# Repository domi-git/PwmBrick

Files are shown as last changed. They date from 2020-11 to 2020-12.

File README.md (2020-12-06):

# PwmBrick

The aim of the project is to create a little box to control a DC-motor. The power should come from a 18650 LiIon-cell and the form-factor should be small.

**This is not a finished product! If you use anything from the project, you use it at your own risk! Be especially careful with the handling of LiIon-Batteries! If you don't know what you're doing there is always the risk of a thermal runaway which could lead to a fire or an explosion!**

## Overview

The current state of the prototype can be seen in the following picture:

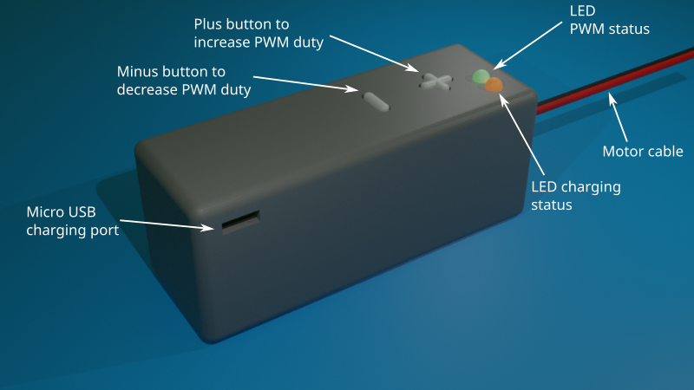
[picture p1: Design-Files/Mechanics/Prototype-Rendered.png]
Prototype-Render


**Main Features:**

| Feature | Value |
|---|---|
| Max. Output Current | 3A |
| Output Voltage (depends on charging status) | 3.4V - 4.2V |
| PWM-States (Can be switched via the buttons) | 4 |
| PWM frequency | 10kHz |
| Undervoltage Lockout (going into) | 3.4V |
| Undervoltage Lockout (leaving) | 3.7V |

## Mechanics

All the CAD-Drawings were carried out with Blender. The assembly consists of the following parts:
* top-part of the housing with cutouts for the buttons, the charging port and the LEDs
* bottom-part of the housing
* fibre-optics to guide the LED light
* plus- and minus-button
* pcb with soldered battery-holder for 18650-cell

You can see the listed parts in the following picture:

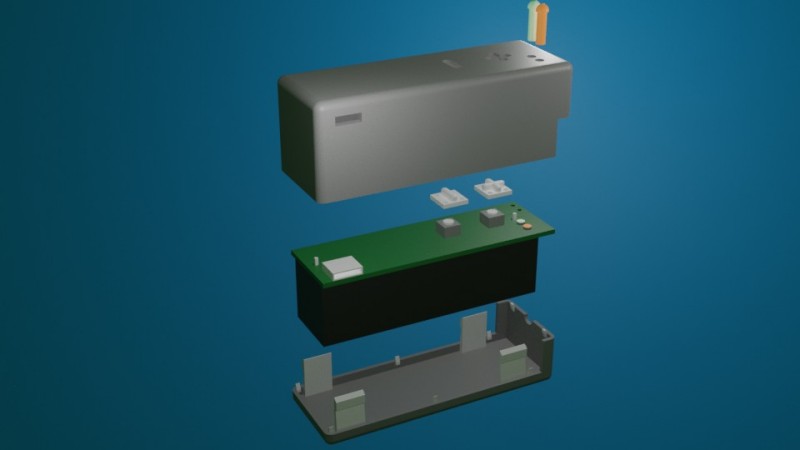
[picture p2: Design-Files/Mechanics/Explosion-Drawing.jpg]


## Electronics

The schematic and the layout was done in KiCad. The goal was to keep the overall space of the electronics very close to the footprint of the battery-holder for the 18650 LiIon cell. 

**Block diagram**

Schematic

**Schematic**

Schematic

**Layout**

Layout-Top
Layout-Bot

## Software

TBD

## Possible improvements

### Documentation
* Snap-Fit Design
* The states of the PWM
* Debugging capabilities with TermControl
* How to flash new software

### Mechanics

* Incoporate a cutout for the micro-usb charging port. At the moment the cable does not fit.

### Electronics

For the current PCB:
* Accurately measure the undervoltage lockout thresholds
* Measure the charging current over time

For next PCB revision:
* Incorporate a way to use the charging LED from the microcontroller (It should not be exclusive to the charging IC)
* Low-pass for the measurement of the battery-voltage
* Pull-Downs/Pull-Ups for the Uart/Flash connector

### Software   

* Clean up the code
* Implement a soft transition of the pwm duty-cycle in state changes
* Replace as much of generated code from the IDE with own implementations

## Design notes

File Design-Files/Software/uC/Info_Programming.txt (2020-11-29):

The controller can be programmed via ST-Link/V2-1. You can use most of the nucleo boards from ST for programming, because they have an integreted programmer (i have the Nucleo-F446RE-Board).

Connection between Nucleo-Board and own PCB
-------------------------------------------
I'm using connector CN4 on the Nucleo-Board, with the following pins:
- VDD
- SWCLK
- GND
- SWDIO
- NRST

You can flash the software with the STM32CubeIDE (just press the "debug"-button).

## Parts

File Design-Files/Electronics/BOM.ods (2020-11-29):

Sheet: Übersicht
Part | MPN | Quantity | Price | Price (sum) | Height | Area mmxmm (incl. Pins) | Link
Microcontroller | STM32F030F4P6 | 1 | 1.40 € | 1.40 € | 1.0 | 6.5x6.5 | https://www.reichelt.de/mcu-arm-32-bit-16-kb-tssop-20-stm-32f030f4p6-p168428.html?&trstct=pos_4
Mosfets | SI4114DY-GE3 | 2 | 0.87 € | 1.74 € | 1.8 | 4.9x6.0 | https://www.reichelt.de/mosfet-n-ch-20v-20a-0-006r-so8-si4114dy-ge3-p254848.html?&trstct=pol_1
Mosfet-Driver | IR2011S | 1 | 2.30 € | 2.30 € | 1.8 | 4.9x6.0 | https://www.reichelt.de/mosfet-treiber-high-and-low-side-so-8-ir-2011s-p129748.html?&trstct=pos_07
Boost-Converter | MAX5026EUT+T | 1 | 1.10 € | 1.10 € | 1.5 | 3.0x3.0 | https://www.reichelt.de/boost-schaltregler-adj-40ma-3-11vi-sot23-6-max5026eut-t-p256372.html?trstct=pol_10
Inductor | L-PIS2408 10µ | 1 | 0.74 € | 0.74 € | 3.2 | 6.6x6.2 | https://www.reichelt.de/smd-power-induktivitaet-pis2408-ferrit-10-l-pis2408-10-p73080.html?trstct=pol_5
Boost Diode | MBR0520LT1 | 1 | 0.08 € | 0.08 € | 1.3 | 2.8x1.8 | https://www.reichelt.de/schottkydiode-20-v-0-5-a-sod-123-mbr-0520lt1g-ons-p219620.html?&trstct=pol_0
Linear Regulator (3.3V) | MCP1700T-2502E/TT | 1 | 0.53 € | 0.53 € | 1.0 | 2.1x2.6 | https://www.conrad.de/de/p/microchip-technology-mcp1700t-2502e-mb-pmic-spannungsregler-linear-ldo-positiv-fest-sot-89-3-1085862.html
Charging-IC | MAX1811 | 1 | 2.75 € | 2.75 € |  |  | https://www.reichelt.de/battery-management-ic-li-lader-so-8-max-1811-esa-p57853.html?&trstct=pos_1
LED orange | KA-3528SECKT | 1 | 0.12 € | 0.12 € | 1.9 | 2.8x3.5 | https://www.conrad.de/de/p/kingbright-ka-3528seckt-smd-led-plcc2-orange-230-mcd-120-20-ma-2-1-1050363.html
LED green | KA-3528CGCKT | 1 | 0.13 € | 0.13 € | 1.9 | 2.8x3.5 | https://www.conrad.de/de/p/kingbright-ka-3528cgckt-smd-led-plcc2-gruen-100-mcd-120-20-ma-2-1-v-1050365.html
Optical Fiber | 1282.1000 | 2 | 0.69 € | 1.38 € | - | - | https://www.conrad.de/de/p/mentor-1282-1000-hohllichtleiter-starr-kartenbefestigung-presspassung-183494.html
Button | RND 210-00203 | 2 | 0.21 € | 0.42 € | 4.3 | 6x6 | https://www.reichelt.de/printtaster-smd-1-57-n-6-x-6-x-4-3-mm-rnd-210-00203-p226424.html?trstct=pol_10
Programming heaeder THT 1.27mm vertically |  | 1 | 0.89 € | 0.89 € | 5.0 |  | https://www.conrad.de/de/p/tru-components-stiftleiste-standard-anzahl-reihen-1-polzahl-je-reihe-20-tc-2506255-1-st-2139366.html
Charging Jack (Micro-USB) |  | 1 | 1.96 € | 1.96 € | 2.6 |  | https://www.conrad.de/de/p/micro-usb-steckverbinder-serie-wr-com-buchse-einbau-vertikal-smt-wuerth-elektronik-inhalt-1-st-1898830.html
Capacitor | X7R-G0603 100N | 1 | 0.02 € | 0.02 € | 1.0 |  | https://www.reichelt.de/smd-vielschicht-keramikkondensator-100n-10-x7r-g0603-100n-p31873.html?trstct=pol_0
Capacitor | KEM X5R0603 1,0U | 1 | 0.02 € | 0.02 € | 1.0 |  | https://www.reichelt.de/vielschicht-kerko-1-0-f-25v-85-c-kem-x5r0603-1-0u-p207006.html?&trstct=pol_1
Capacitor | KEM X5R0603 4,7U | 4 | 0.07 € | 0.28 € | 1.0 |  | https://www.reichelt.de/vielschicht-kerko-4-7-f-10v-85-c-kem-x5r0603-4-7u-p207009.html?&trstct=pol_0
Quarz 8MHz | 8.000MHZ MQ 30/30/40/12PF | 1 | 2.21 € | 2.21 € | 1.2 | 5x7 | https://www.conrad.de/de/p/euroquartz-quarzkristall-quarz-smd-5x7-smd-4-8-000-mhz-12-pf-7-mm-5-mm-1-2-mm-1-st-155131.html
Capacitor 4pF Quarz | NPO 0603 CF 4,0P | 1 | 0.02 € | 0.02 € |  |  | https://www.reichelt.de/smd-kerko-0603-4-0pf-50v-10-mlcc-npo-0603-cf-4-0p-p193988.html?&trstct=pol_0
Fuse (not recommended, but footprint in PCB v4) | 220034 | 1 | 0.69 € | 0.69 € |  | 3x7 | https://www.conrad.de/de/p/eska-smd-ssq-f-3-a-smd-sicherung-smd-2410-3-a-125-v-flink-f-1-529794.html
Fuse (recommended and in use in PCB v4) | MINISMDC150F-2 | 1 | 0.04 € | 0.04 € |  |  | https://lcsc.com/product-detail/Surface-Mount-Fuses_TE-Connectivity_MINISMDC150F-2_1-5A-6V_C9308.html
Programming header THT 1.27mm horizontal | TC-1414-20-2-20-00 | 1 | 1.30 € | 1.30 € | 2.1 |  | https://www.conrad.de/de/p/w-p-products-stiftleiste-standard-anzahl-reihen-1-polzahl-je-reihe-20-707-1-20-2-20-00-1-719680.html
Resistor 0 Ohm | RND 0805 0 | 3 | 0.02 € | 0.06 € |  |  | https://www.reichelt.de/smd-widerstand-0805-0-ohm-125-mw-rnd-0805-0-p183146.html?&nbc=1
Various other Resistors in 0805, see schematic (I have them laying around)

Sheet: Lade-IC
Bauteil | MPN | Preis | Features | Bedenken | Link
Lade-IC | MAX1555 | 2.02 € | 100mA, Eingangsspannung OK, Ladestatus, UVLO-Eingang, 4.2V Full | Thermik? | https://www.conrad.de/de/p/maxim-integrated-max1555ezk-t-pmic-batteriemanagement-lademanagement-li-ion-li-pol-tsot-23-5-oberflaechenmontage-1121936.html
Lade-IC | MCP73833-FCI/UN | 0.86 € | Temp Monitor, Programmable Full-Voltage, CC und CV-Ladung, Programmable Charge Current, Ladestatus |  | https://www.conrad.de/de/p/microchip-technology-mcp73833-fci-un-pmic-batteriemanagement-lademanagement-li-ion-li-pol-msop-10-oberflaechenmontage-1085504.html
Lade-IC | MAX1811 | 2.75 € | 4.1/4.2 Full, Ladestatus, Enable, SO-8 Package, 100mA oder 500mA |  | https://www.reichelt.de/battery-management-ic-li-lader-so-8-max-1811-esa-p57853.html?&trstct=pos_1
Lade-IC | BQ24090 | 1.25 € | 100mA oder 500mA, Sicherheitstimer (10h), CC und CV-Ladung, Ausgangskurzschlusserkennung, Termistor Pin, Ladestatus, Power Good |  | https://www.reichelt.de/battery-management-ic-li-ion-msop-10-bq-24090-dgqt-p188799.html?trstct=pos_0
Lade-IC | MC34671AEPR2 | 1.39 € | 600mA, |  | https://www.conrad.de/de/p/nxp-semiconductors-mc34671aepr2-pmic-batteriemanagement-lademanagement-li-ion-li-pol-udfn-8-ep-2x3-oberflaechenmonta-1182980.html

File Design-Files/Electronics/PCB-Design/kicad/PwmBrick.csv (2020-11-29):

Id | Designator | Package | Quantity | Designation | Supplier and ref
1 | J1 | battery_holder_18650 | 1 | Conn_01x02
2 | R4,R13 | R_0805_2012Metric_Pad1.15x1.40mm_HandSolder | 2 | 270R
3 | TP2,TP1 | TestPoint_Pad_1.0x1.0mm | 2 | TestPoint
4 | R8,R12,R11 | R_0805_2012Metric_Pad1.15x1.40mm_HandSolder | 3 | 10k
5 | R7 | R_0805_2012Metric_Pad1.15x1.40mm_HandSolder | 1 | 120k
6 | R6 | R_0805_2012Metric_Pad1.15x1.40mm_HandSolder | 1 | 100k
7 | J4 | PinHeader_1x06_P1.27mm_Horizontal | 1 | Conn_01x06_Male
8 | F1 | Fuse_2512_6332Metric | 1 | Fuse
9 | R9,R10,R5 | R_0805_2012Metric_Pad1.15x1.40mm_HandSolder | 3 | 0R
10 | C15,C16,C9,C10,C17 | C_0603_1608Metric_Pad1.05x0.95mm_HandSolder | 5 | 100n
11 | U5 | SO-8_3.9x4.9mm_P1.27mm | 1 | IR2011
12 | C14,C8,C6,C5,C4 | C_0603_1608Metric_Pad1.05x0.95mm_HandSolder | 5 | 1u
13 | U4 | TSSOP-20_4.4x6.5mm_P0.65mm | 1 | STM32F030F4Px
14 | C7,C11,C2,C1 | C_0603_1608Metric_Pad1.05x0.95mm_HandSolder | 4 | 4u7
15 | C12,C13 | C_0603_1608Metric_Pad1.05x0.95mm_HandSolder | 2 | 4p
16 | Y1 | Crystal_SMD_EuroQuartz_MQ-4Pin_7.0x5.0mm | 1 | Crystal_GND24
17 | R3,R1 | R_0805_2012Metric_Pad1.15x1.40mm_HandSolder | 2 | 47k
18 | R2 | R_0805_2012Metric_Pad1.15x1.40mm_HandSolder | 1 | 330k
19 | Q2,Q1 | SOIC-8-SI4114DY-GE3 | 2 | Q_NMOS_DGS
20 | SW2,SW1 | SW_Push_1P1T_NO_6x6mm_H9.5mm | 2 | SW_Push
21 | U1 | TSOT-23-6 | 1 | MAX5026EUT
22 | J3 | Motor_Connector | 1 | Conn_01x02
23 | J2 | USB_Micro-B_Wuerth_629105150521 | 1 | USB_B_Micro
24 | L1 | L_6.3x6.3_H3 | 1 | 10u
25 | D4,D2 | LED_PLCC-2 | 2 | LED
26 | D1,D3 | D_SOD-123 | 2 | MBR0520LT
27 | U2 | SOT-89-3 | 1 | MCP1700-2502E_SOT89
28 | U3 | SOIC-8_3.9x4.9mm_P1.27mm | 1 | MAX1811

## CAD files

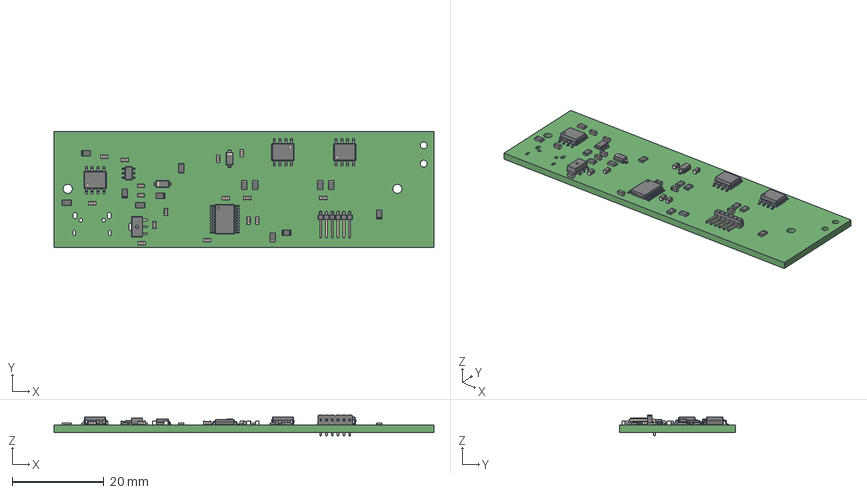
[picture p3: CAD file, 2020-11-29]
Design-Files/Mechanics/blender/kicad-export/pcb.step
83.0 x 25.3 x 4.50 mm
switch x 2

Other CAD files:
Design-Files/Mechanics/blender/assembly.blend

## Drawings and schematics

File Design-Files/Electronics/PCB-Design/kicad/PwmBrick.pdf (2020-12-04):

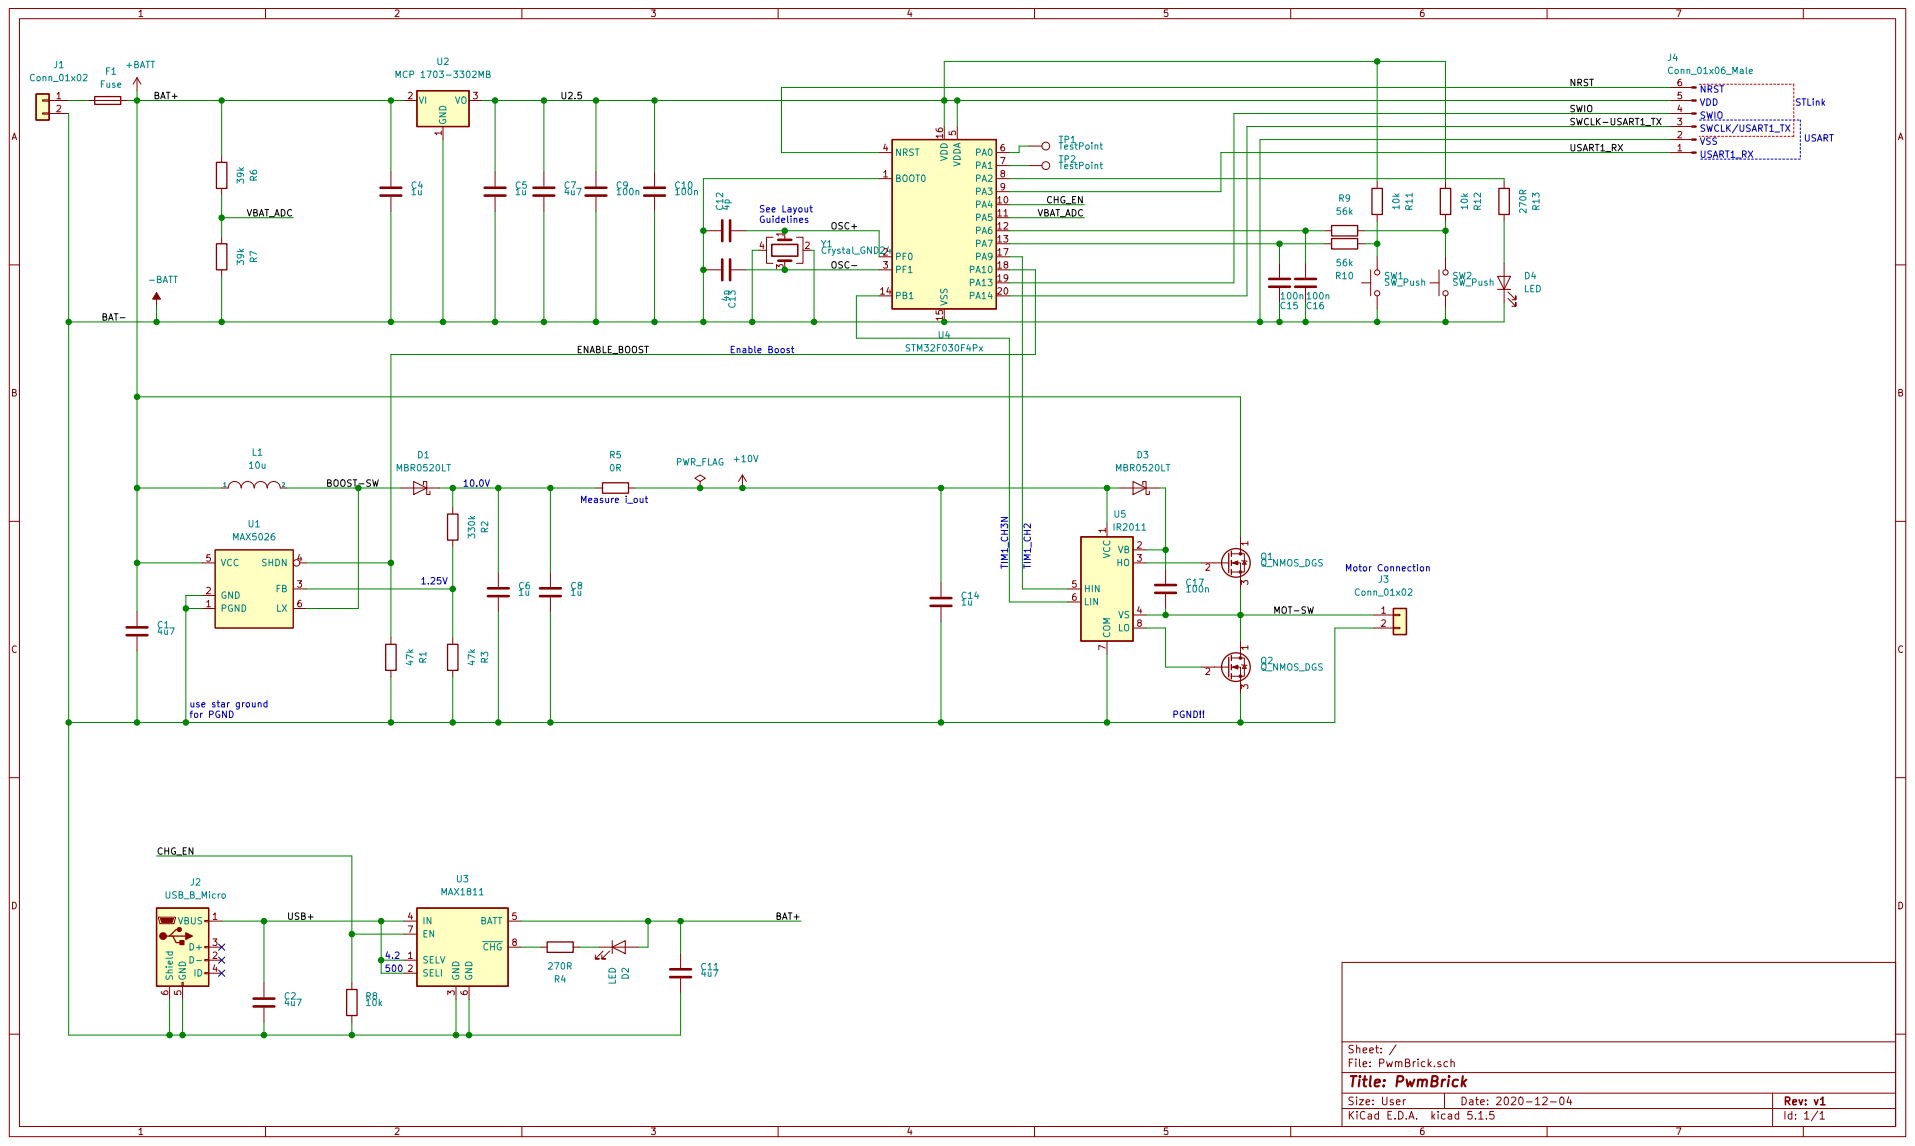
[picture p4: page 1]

1 VB 2 HO 3 VS 4 HIN 5

File: PwmBrick.sch Sheet: /
Id: 1/1 Title: PwmBrick

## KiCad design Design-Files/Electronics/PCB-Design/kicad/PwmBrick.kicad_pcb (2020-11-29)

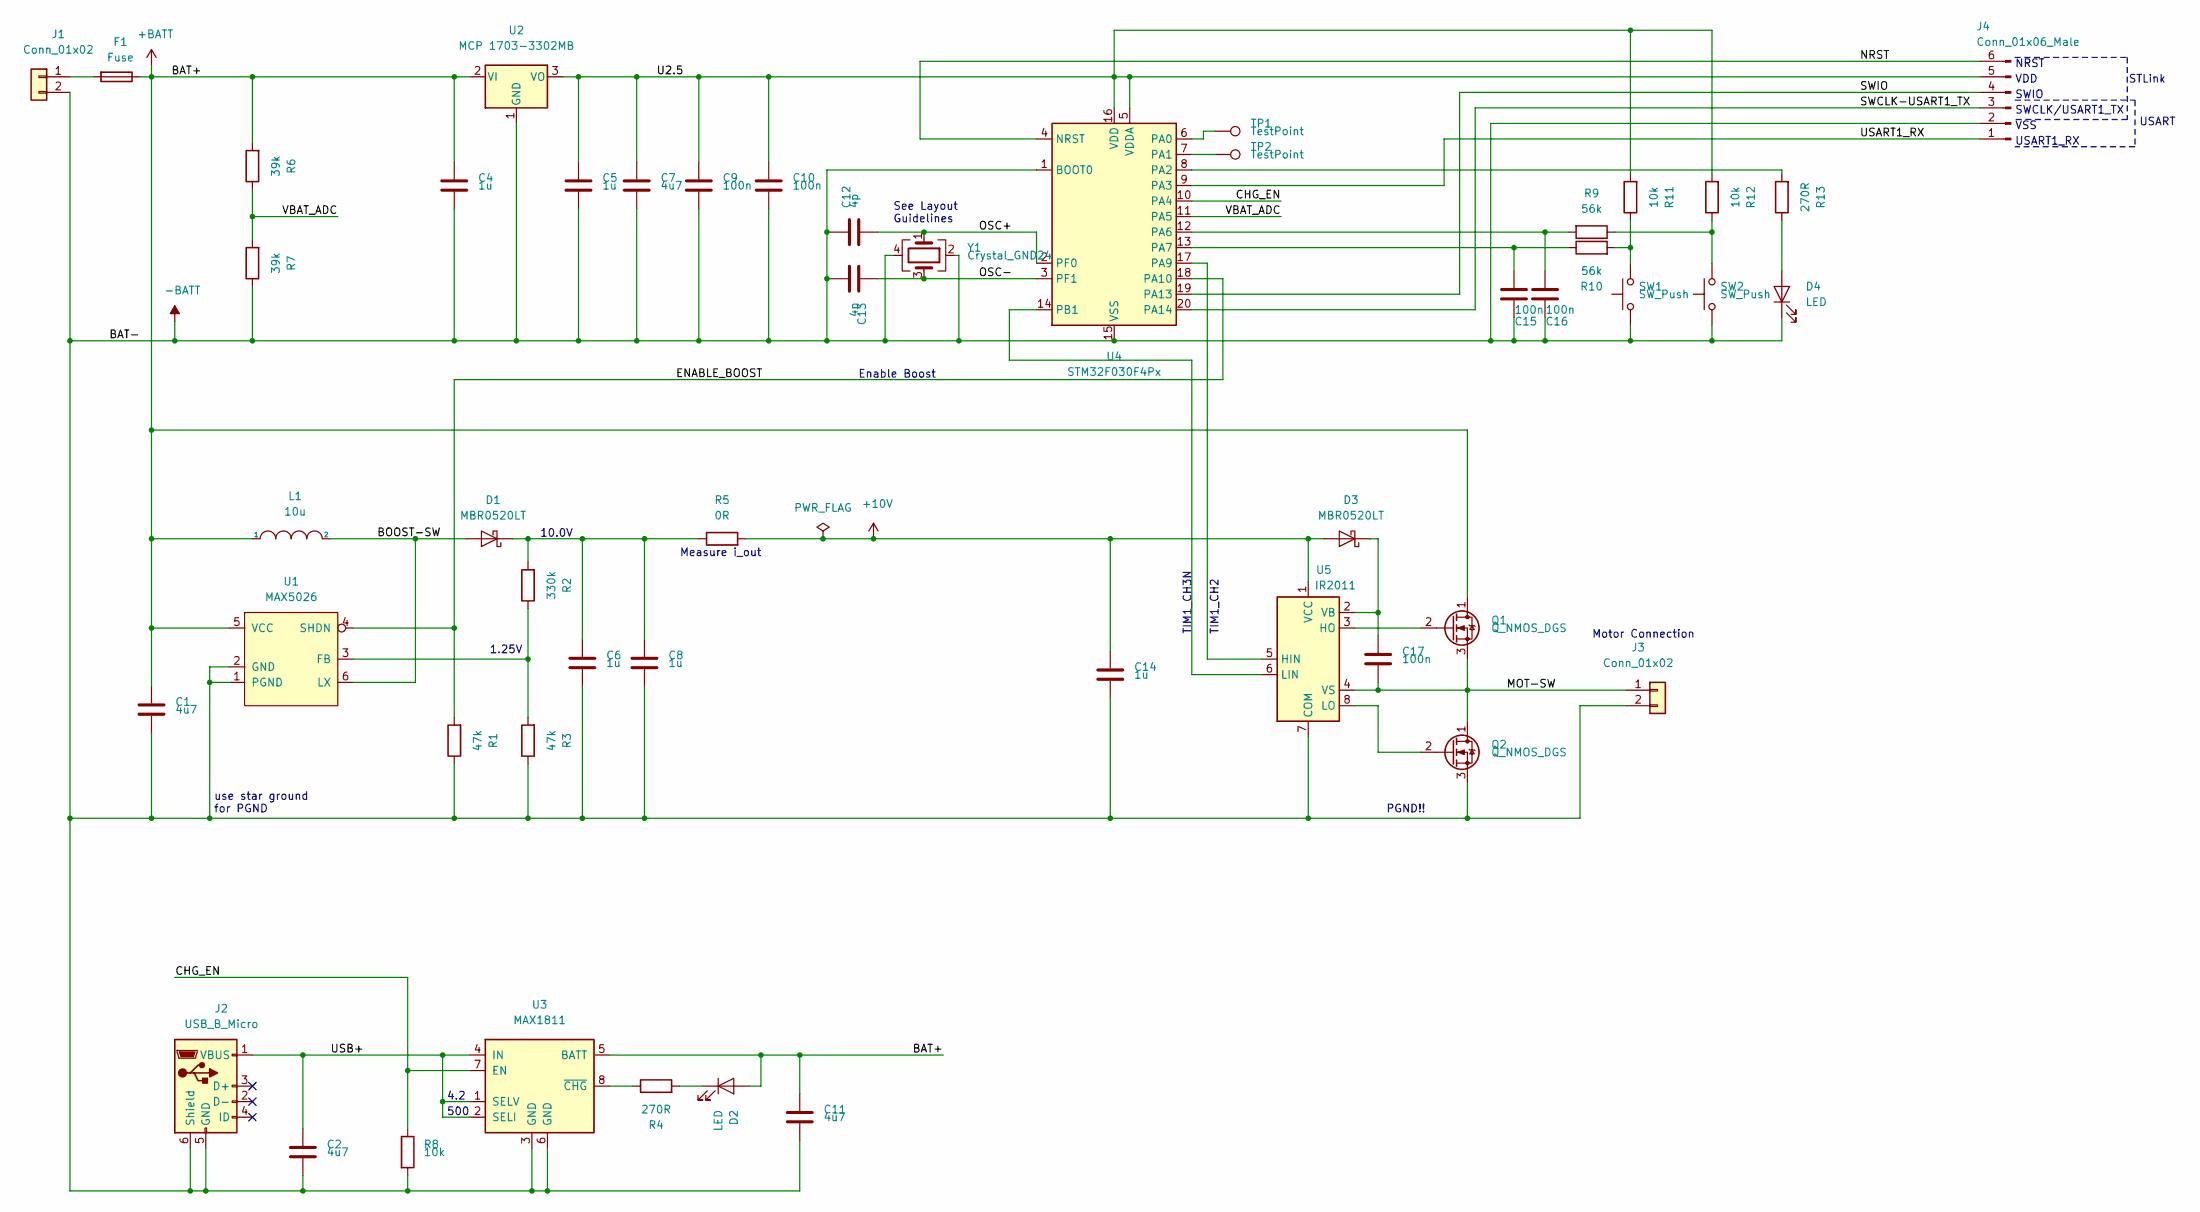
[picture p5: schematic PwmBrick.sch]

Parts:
C1, C2, C7, C11: 4u7; C_0603_1608Metric_Pad1.05x0.95mm_HandSolder
C4, C5, C6, C8, C14: 1u; C_0603_1608Metric_Pad1.05x0.95mm_HandSolder
C9, C10, C15, C16, C17: 100n; C_0603_1608Metric_Pad1.05x0.95mm_HandSolder
C12, C13: 4p; C_0603_1608Metric_Pad1.05x0.95mm_HandSolder
D1, D3: MBR0520LT; D_SOD-123
D2, D4: LED; LED_PLCC-2
F1: Fuse; Fuse_2512_6332Metric
J1: Conn_01x02; battery_holder_18650
J2: USB_B_Micro; USB_Micro-B_Wuerth_629105150521
J3: Conn_01x02; Motor_Connector
J4: Conn_01x06_Male; PinHeader_1x06_P1.27mm_Horizontal
L1: 10u; L_6.3x6.3_H3
Q1, Q2: Q_NMOS_DGS; SOIC-8-SI4114DY-GE3
R1, R3: 47k; R_0805_2012Metric_Pad1.15x1.40mm_HandSolder
R2: 330k; R_0805_2012Metric_Pad1.15x1.40mm_HandSolder
R4, R13: 270R; R_0805_2012Metric_Pad1.15x1.40mm_HandSolder
R5: 0R; R_0805_2012Metric_Pad1.15x1.40mm_HandSolder
R6, R7: 39k; R_0805_2012Metric_Pad1.15x1.40mm_HandSolder
R8, R11, R12: 10k; R_0805_2012Metric_Pad1.15x1.40mm_HandSolder
R9, R10: 56k; R_0805_2012Metric_Pad1.15x1.40mm_HandSolder
SW1, SW2: SW_Push; SW_Push_1P1T_NO_6x6mm_H9.5mm
TP1, TP2: TestPoint; TestPoint_Pad_1.0x1.0mm
U1: MAX5026; TSOT-23-6
U2: MCP 1703-3302MB; SOT-89-3
U3: MAX1811; SOIC-8_3.9x4.9mm_P1.27mm
U4: STM32F030F4Px; TSSOP-20_4.4x6.5mm_P0.65mm
U5: IR2011; SO-8_3.9x4.9mm_P1.27mm
Y1: Crystal_GND24; Crystal_SMD_EuroQuartz_MQ-4Pin_7.0x5.0mm

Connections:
+10V: C14.1, D3.2 (A), R5.2, U5.1 (VCC)
+BATT: C1.1, C4.1, C11.1, D2.2 (A), F1.1, L1.1, Q1.1 (D), R6.2, U1.5 (VCC), U2.2 (VI), U3.5 (BATT)
-BATT: C1.2, C2.2, C4.2, C5.2, C6.2, C7.2, C8.2, C9.2, C10.2, C11.2, C12.1, C13.2, C14.2, C15.2, C16.2, D4.1 (K), J1.2, J2.5 (GND), J2.6 (Shield), J3.2, J4.2, Q2.3 (S), R1.1, R3.1, R7.1, R8.2, SW1.1, SW2.1, U1.1 (PGND), U1.2 (GND), U2.1 (GND), U3.3 (GND), U3.6 (GND), U4.1 (BOOT0), U4.15 (VSS), U5.7 (COM), Y1.2, Y1.4
/BOOST-SW: D1.2 (A), L1.2, U1.6 (LX)
/CHG_EN: R8.1, U3.7 (EN), U4.10 (PA4)
/ENABLE_BOOST: R1.2, U1.4 (SHDN), U4.18 (PA10)
/MOT-SW: C17.2, J3.1, Q1.3 (S), Q2.1 (D), U5.4 (VS)
/NRST: J4.6, U4.4 (NRST)
/OSC+: C12.2, U4.2 (PF0), Y1.1
/OSC-: C13.1, U4.3 (PF1), Y1.3
/SWCLK-USART1_TX: J4.3, U4.20 (PA14)
/SWIO: J4.4, U4.19 (PA13)
/U2.5: C5.1, C7.1, C9.1, C10.1, J4.5, R11.2, R12.2, U2.3 (VO), U4.5 (VDDA), U4.16 (VDD)
/USART1_RX: J4.1, U4.9 (PA3)
/USB+: C2.1, J2.1 (VBUS), U3.1 (SELV), U3.2 (SELI), U3.4 (IN)
/VBAT_ADC: R6.1, R7.2, U4.11 (PA5)
unnamed: C6.1, C8.1, D1.1 (K), R2.2, R5.1
unnamed: C15.1, R10.1, U4.13 (PA7)
unnamed: C16.1, R9.2, U4.12 (PA6)
unnamed: C17.1, D3.1 (K), U5.2 (VB)
unnamed: D2.1 (K), R4.2
unnamed: D4.2 (A), R13.1
unnamed: F1.2, J1.1
unnamed: Q1.2 (G), U5.3 (HO)
unnamed: Q2.2 (G), U5.8 (LO)
unnamed: R2.1, R3.2, U1.3 (FB)
unnamed: R4.1, U3.8 (~CHG)
unnamed: R10.2, R11.1, SW1.2
unnamed: R9.1, R12.1, SW2.2
unnamed: R13.2, U4.8 (PA2)
unnamed: TP1.1, U4.6 (PA0)
unnamed: TP2.1, U4.7 (PA1)
unnamed: U4.14 (PB1), U5.6 (LIN)
unnamed: U4.17 (PA9), U5.5 (HIN)

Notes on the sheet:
Motor Connection
See Layout Guidelines
1.25V
use star ground for PGND
10.0V
Measure i_out
Enable Boost
PGND!!
TIM1_CH3N
TIM1_CH2
USART1_RX
VSS
VDD
SWIO
NRST
STLink
500
4.2
SWCLK/USART1_TX
USART

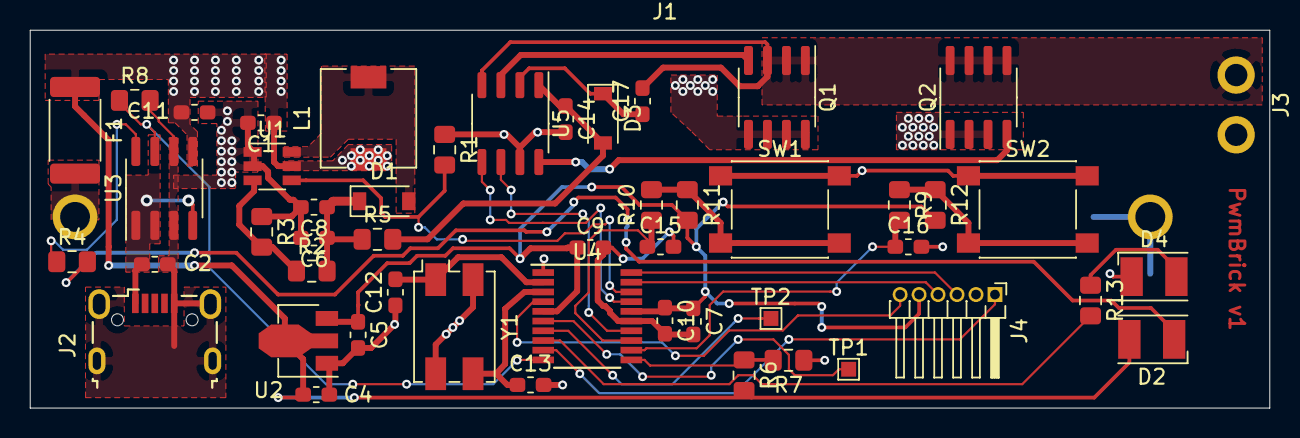
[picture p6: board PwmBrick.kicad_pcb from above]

Board: 2 copper layers, 83.0 x 25.3 mm, 51 parts (0 on the bottom side), 34 nets.

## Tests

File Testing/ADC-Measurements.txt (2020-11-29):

U / mV	Digits
1034		1300
840			1043
579			685
347			370
282			288

Octave-Code:
------------
u2=[1034 840 579 347 282]
dig2=[1300 1043 685 370 288]
plot(u2, dig2)
xlabel('Voltage in mV')
ylabel('Digits')
grid on

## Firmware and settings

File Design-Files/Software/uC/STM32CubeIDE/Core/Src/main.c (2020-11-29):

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

/* Includes ------------------------------------------------------------------*/
#include "main.h"

/* USER CODE BEGIN Includes */
#include "uart.h"
#include "term.h"

/* USER CODE END Includes */

/* USER CODE BEGIN PD */

/* Battery-Voltage Measurement: Convert ADC-Digits to Voltage */
#define  DIG_VOLT  657u / 4095u

/* USER CODE END PD */

ADC_HandleTypeDef hadc;

TIM_HandleTypeDef htim1;

/* USER CODE BEGIN PV */
uint32_t state = 0u;					// State of the System

uint32_t tickTmp = 0u;				// Systick-Value from Last Input readings
uint32_t termTick = 0u;       // Number of 100ms ticks between since the last call of CycleTerm

uint32_t chgTick = 0u;				// Number of 100ms ticks the Up-Button is pressed
uint32_t chgModeChange = 0u;	// Remember, if charger mode was changed before

uint32_t upTmp = 0u;					// Last Position of Up-Button
uint32_t downTmp = 0u;				// Last Position of Down-Button

uint32_t flashCnt = 0u;				// Current number of LED-flashes within the blink-code

uint32_t usartEnable = 0u;    // Is USART1 started?
uint32_t usartDelay = 0u;     // Current Delay if USART isn't started yet (in multiples of 100ms)

uint32_t adcVal = 0u;					// Raw ADC-Value for Battery-Voltage (12-Bit)
uint32_t batVolt = 0u;        // Battery-Voltage from ADC in 0.01V
uint32_t recharge = 0u;       // 1=recharge state (Battery Voltage too low), 0=no recharge state


/* USER CODE END PV */

void SystemClock_Config(void);
static void MX_GPIO_Init(void);
static void MX_TIM1_Init(void);
static void MX_ADC_Init(void);
/* USER CODE BEGIN PFP */
static void InitUsart1Tx(void);
static void InitPWM(void);
static void CycleUpBtn(void);
static void CycleDownBtn(void);
static void CycleLedDisplay(void);
static void CycleAdc(void);
/* USER CODE END PFP */

/**
  * @brief  The application entry point.
  * @retval int
  */
int main(void)
{
  

  /* MCU Configuration--------------------------------------------------------*/

  /* Reset of all peripherals, Initializes the Flash interface and the Systick. */
  HAL_Init();

  /* Configure the system clock */
  SystemClock_Config();

  /* Initialize all configured peripherals */
  MX_GPIO_Init();
  MX_TIM1_Init();
  MX_ADC_Init();
  /* USER CODE BEGIN 2 */

  /* Initialize ADC-Periphal -> Channel 5 */
  //InitAdc();

  /* Additional Init-Code for the PWM with Deadtime */
  InitPWM();

  /* Start 10V-Regulator (For Mosfet Driver) */
  HAL_GPIO_WritePin(GPIOA, GPIO_PIN_10, GPIO_PIN_SET);

  /* USER CODE END 2 */

  /* Infinite loop */
  /* USER CODE BEGIN WHILE */
  /* Infinite loop */
  while (1)
  {
    /* USER CODE END WHILE */

    /* USER CODE BEGIN 3 */

  	/*  Loop every 100ms */
  	if (HAL_GetTick() > tickTmp + 100u)
		{
			tickTmp = HAL_GetTick();

			/* Up-Button Handling */
			CycleUpBtn();

			/* Down-Button handling */
			CycleDownBtn();

			/* ADC-Handling (Get Battery-Voltage) */
			CycleAdc();

			/* Handle State-Changes for Battery-Undervoltage */
			if (batVolt > 0u)  /* Only check, if there has been a battery Voltage Measurement */
			{
				/* Voltage too low? => recharge state */
				if (recharge == 0u && batVolt < 340)
				{
					recharge = 1u;
				}
				/* If recharge state and battery voltage high enough => quit recharge state */
				else if (recharge == 1u && batVolt > 370)
				{
					recharge = 0u;
					state = 0u;
				}
			}

			/* No PWM in recharge state and 10x-Blink-Code */
			if (recharge == 0u)
			{
				/* Handle PWM-Duty */
				TIM1->CCR2 = state*595u;
				TIM1->CCR3 = state*595u;
			}
			else
			{
				TIM1->CCR2 = 0u;
				TIM1->CCR3 = 0u;
				state = 10u;
			}

			/* Enable USART after 10 seconds (no more programming possible, because SWCLK-Pin is used!) */
			if (usartEnable == 0u)
			{
				if (usartDelay < 100u)
				{
					usartDelay++;
				}
				else
				{
					usartEnable = 1u;
					InitUsart1Tx();
					InitUart();
				}
			}
			else
			{
				termTick++;
				if (termTick >= 2u)
				{
					termTick = 0u;
					CycleTerm();
				}
			}

	  	/* Display state as LED-blinking code */
			CycleLedDisplay();

		} /* 100ms */
  } /* while */

  /* USER CODE END 3 */
}

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
/* USER CODE BEGIN 4 */

/*----------------------------------------------------------------------------*/
static void InitUsart1Tx(void)
{
  GPIO_InitTypeDef GPIO_InitStruct = {0};

  /*Configure GPIO pin : PA3 */
  GPIO_InitStruct.Pin = GPIO_PIN_14;
  GPIO_InitStruct.Mode = GPIO_MODE_AF_PP;
  GPIO_InitStruct.Pull = GPIO_NOPULL;
  GPIO_InitStruct.Speed = GPIO_SPEED_FREQ_HIGH;
  GPIO_InitStruct.Alternate = GPIO_AF1_USART1;
  HAL_GPIO_Init(GPIOA, &GPIO_InitStruct);

}

/*----------------------------------------------------------------------------*/
static void InitPWM(void)
{
  /* Komplementären Ausgang von Channel 3 und Channel 2 aktivieren, wird von der Library nicht gemacht! */
  /* Der negative Ausgang von Channel 2 muss auch aktiviert werden, damit die Totzeit dort wirksam wird */
  TIM_CCxChannelCmd(TIM1, TIM_CHANNEL_3, TIM_CCxN_ENABLE);
  TIM_CCxChannelCmd(TIM1, TIM_CHANNEL_2, TIM_CCxN_ENABLE);

  /* Konfiguration der Verriegelungszeit nochmal durchführen. Code-Generierung kann nur Deadtime = 0 generieren... */
  TIM_BreakDeadTimeConfigTypeDef sBreakDeadTimeConfig = {0};
  sBreakDeadTimeConfig.OffStateRunMode = TIM_OSSR_DISABLE;
  sBreakDeadTimeConfig.OffStateIDLEMode = TIM_OSSI_DISABLE;
  sBreakDeadTimeConfig.LockLevel = TIM_LOCKLEVEL_OFF;
  sBreakDeadTimeConfig.DeadTime = 5;
  sBreakDeadTimeConfig.BreakState = TIM_BREAK_ENABLE;
  sBreakDeadTimeConfig.BreakPolarity = TIM_BREAKPOLARITY_HIGH;
  sBreakDeadTimeConfig.AutomaticOutput = TIM_AUTOMATICOUTPUT_ENABLE;
  HAL_TIMEx_ConfigBreakDeadTime(&htim1, &sBreakDeadTimeConfig);

  /* Start PWM */
  HAL_TIM_PWM_Start(&htim1, TIM_CHANNEL_2);
  HAL_TIM_PWM_Start(&htim1, TIM_CHANNEL_3);
}

/*----------------------------------------------------------------------------*/
static void CycleUpBtn (void)
{
	// Up-Button handling
	if (upTmp == 0u)
	{
		// If Up-Button wasn't pressed before and is pressed now => change upTmp
		if (HAL_GPIO_ReadPin(GPIOA, Switch_Plus_Pin) == GPIO_PIN_RESET)
		{
			upTmp = 1u;
		}
	}
	else  // Button was pressed before
	{
		// If Up-Button was pressed and is'nt pressed now => change state
		if (HAL_GPIO_ReadPin(GPIOA, Switch_Plus_Pin) == GPIO_PIN_SET)
		{
			if (chgModeChange == 0u)  // Only handle state changes when charge mode is not changed
			{
				// If Up-Button is now pressed and wasn't pressed before => next state and remember it is pressed
				upTmp = 0u;
				// Next state and overflow handling
				if (state <= 3u)
				{
					state++;
				}
				else
				{
					state = 4u;
				}
			}
			else
			{
				upTmp = 0u;
				chgModeChange = 0u;
			}
		}
		// Up-Button is still pressed
		else
		{
			chgTick++;
			// If Up-Button is pressed for 2 seconds => Toggle Charge mode
			if (chgTick > 20u)
			{
				chgTick = 0u;
				chgModeChange = 1u;
				HAL_GPIO_TogglePin(GPIOA, GPIO_PIN_4);
			}
		}
	}
}

/*----------------------------------------------------------------------------*/
static void CycleDownBtn (void)
{
	if (downTmp == 0u)
	{
		// If Down-Button is now pressed and wasn't pressed before => next state and remember it is pressed
		if (HAL_GPIO_ReadPin(GPIOA, Switch_Minus_Pin) == GPIO_PIN_RESET)
		{
			downTmp = 1u;
			// Next state and overflow handling
			if (state >= 1u)
			{
				state--;
			}
			else
			{
				state = 0u;
			}
		}
	}
	else
	{
		// If Down-Button is not pressed and was pressed before => just remember it isn't pressed
		if (HAL_GPIO_ReadPin(GPIOA, Switch_Plus_Pin) == GPIO_PIN_SET)
		{
			downTmp = 0u;
		}
	}
}

/*----------------------------------------------------------------------------*/
static void CycleLedDisplay (void)
{
	if (state == 0u)
	{
		flashCnt = 0u;
		HAL_GPIO_WritePin(GPIOA, LED_Green_Pin, GPIO_PIN_RESET);
	}
	else
	{
		if (flashCnt >= 100u)  // long off-interval
		{
			flashCnt++;
			if (flashCnt > 105u) { flashCnt = 0u; }
		}
		else  // Blink-code
		{
			flashCnt++;
			HAL_GPIO_TogglePin(GPIOA, LED_Green_Pin);
			if (flashCnt >= 2u*state)
			{
				flashCnt = 100u;  // Start long off-interval
			}
		}
	} // LED-blinking code
}

/*----------------------------------------------------------------------------*/
static void CycleAdc (void)
{
	HAL_ADC_Start(&hadc);
	HAL_ADC_PollForConversion(&hadc, 5u);
	adcVal = HAL_ADC_GetValue(&hadc);
	HAL_ADC_Stop(&hadc);
	batVolt = adcVal * DIG_VOLT;
}

/*----------------------------------------------------------------------------*/

/* USER CODE END 4 */
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


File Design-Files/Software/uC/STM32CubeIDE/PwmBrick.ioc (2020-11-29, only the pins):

Mcu.UserName=STM32F030F4Px
PA10.GPIO_Label=Start_10V
PA10.Signal=GPIO_Output
PA2.GPIO_Label=LED_Green
PA2.Signal=GPIO_Output
PA3.Signal=USART1_RX
PA4.GPIO_Label=Charge_Enable
PA4.Signal=GPIO_Output
PA5.Signal=ADC_IN5
PA6.GPIO_Label=Switch_Plus
PA6.Signal=GPIO_Input
PA7.GPIO_Label=Switch_Minus
PA7.Signal=GPIO_Input
PA9.GPIO_Label=Pwm_Mos_High
PA9.Signal=S_TIM1_CH2
PB1.GPIO_Label=Pwm_Mos_Low
PB1.Signal=TIM1_CH3N
PF0-OSC_IN.Signal=RCC_OSC_IN
PF1-OSC_OUT.Signal=RCC_OSC_OUT

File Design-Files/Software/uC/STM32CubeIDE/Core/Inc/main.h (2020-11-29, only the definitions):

#define LED_Green_Pin GPIO_PIN_2
#define LED_Green_GPIO_Port GPIOA
#define Charge_Enable_Pin GPIO_PIN_4
#define Charge_Enable_GPIO_Port GPIOA
#define Switch_Plus_Pin GPIO_PIN_6
#define Switch_Plus_GPIO_Port GPIOA
#define Switch_Minus_Pin GPIO_PIN_7
#define Switch_Minus_GPIO_Port GPIOA
#define Pwm_Mos_Low_Pin GPIO_PIN_1
#define Pwm_Mos_Low_GPIO_Port GPIOB
#define Pwm_Mos_High_Pin GPIO_PIN_9
#define Pwm_Mos_High_GPIO_Port GPIOA
#define Start_10V_Pin GPIO_PIN_10
#define Start_10V_GPIO_Port GPIOA
#define OS_NAME_VER  "PwmBrick v1.00  "  /* 16-Character String for OS-Name and Version */

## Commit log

2020-11-29 Changed the LDO for the microcontroller from the old 2.5V to the new 3.3V
    [PwmBrick.sch]
2020-11-29 Added new content to readme
    [PwmBrick.kicad_pcb, assembly.blend, minus_btn.blend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]
2020-11-29 Improvements for the Readme
    [assembly.blend]
2020-11-29 - Added a dummy Cable to the mechanics-CAD to show the connection to the motor - Changed the Readme
    [assembly.blend]
2020-11-29 Readme again
    [assembly.blend]
2020-12-01 Added explosion-drawing to mechanics-CAD and the readme
    [assembly.blend]
2020-12-04 Started with Block Diagram Added Schematic to the Readme
    [PwmBrick.sch, assembly.blend]
2021-02-07 Mechanical Improvements: - Made the micro-usb cutout larger to fit the connector - Made the diameter for the fibre-optics cutouts for the LEDs larger
    [assembly.blend]

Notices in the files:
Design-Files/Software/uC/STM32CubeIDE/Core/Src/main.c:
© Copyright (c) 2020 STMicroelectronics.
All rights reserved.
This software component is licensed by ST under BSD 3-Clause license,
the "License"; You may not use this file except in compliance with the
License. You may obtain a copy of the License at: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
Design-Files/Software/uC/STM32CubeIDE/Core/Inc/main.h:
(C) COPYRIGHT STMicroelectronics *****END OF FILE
